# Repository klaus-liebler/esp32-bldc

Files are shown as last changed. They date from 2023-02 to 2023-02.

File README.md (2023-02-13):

# esp32-bldc - a bldc controller for stationary applications

* Main components are ESP32-S3, DRV8323HRTAR, 6x IRF7480

* Intgrated synchronous step down converter
* CAN-BUS, RS485 (both with switchable termination)
* USB-C, I2C
* All ceramic capacitors
* Power-LED
* Reset Button, Boot Button
* Thermal sensor
* breakable connector area
* optional MT6816 at the bottom PCB side
* parts available at jlcpcb, (5pcs = 113€)
* various GPIO; especially for external magnetic sensor
* desinged with [KiCad](https://www.kicad.org/) with [https://simplefoc.com/](https://simplefoc.com/) in mind
* Four mounting holes
* dimensions 60mm x 52mm (63mm with big connectors)
* currently COMPLETELY untested

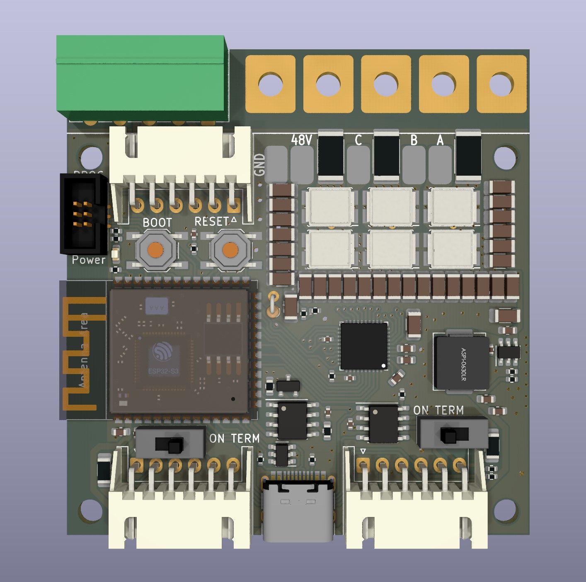
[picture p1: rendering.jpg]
This is an image


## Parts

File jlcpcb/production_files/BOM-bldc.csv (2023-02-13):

Comment | Designator | Footprint | LCSC
1k | R29 | R_0402_1005Metric | C11702
SN65HVD230 | U6 | SOIC-8_3.9x4.9mm_P1.27mm | C12084
10uH | L1 | L_Abracon_ASPI-0630LR | C132141
10u/50V | C1,C10,C11,C12,C13,C14,C15,C16,C17,C18,C19,C2,C20,C28,C29,C3,C30,C31,C32,C38,C4,C5,C6,C7,C8,C9 | C_1206_3216Metric | C13585
u1/50V | C21,C26 | C_0603_1608Metric | C14663
IRF7480M | Q1,Q2,Q3,Q4,Q5,Q6 | DirectFET_ME | C152356
u1 | C22,C27,C33,C35,C41,C42 | C_0402_1005Metric | C1525
1u/50V | C23 | C_0603_1608Metric | C15849
47n/50V | C24 | C_0603_1608Metric | C1622
USB_C_Receptacle_USB2.0 | J8 | USB_C_Receptacle_HRO_TYPE-C-31-M-12 | C165948
1k | R25,R26 | R_0603_1608Metric | C21190
Power | D7 | LED_0603_1608Metric | C2286
k1 | R11 | R_0402_1005Metric | C25076
k22 | R13 | R_0402_1005Metric | C25091
10k | R12,R18,R30,R9 | R_0402_1005Metric | C25744
15k | R7 | R_0402_1005Metric | C25756
22k | R28 | R_0402_1005Metric | C25768
47k | R6 | R_0402_1005Metric | C25792
4k7 | R14,R15 | R_0402_1005Metric | C25900
5k1 | R4,R5 | R_0402_1005Metric | C25905
TP6841S6 | U3 | TSOT-23-6 | C2844736
ESP32-S3-WROOM-1 | U2 | ESP32-S3-WROOM-1 | C2913199
RESET | SW2,SW4 | SW_SPST_TL3342 | C318884
PSM712 | D1 | SOT-23_smaller_withoutSilkscreen | C32677
1u/6V3 | C25 | C_0402_1005Metric | C52923
22u | C36,C37,C40 | C_0603_1608Metric | C59461
DRV8323HRTAR | U1 | Texas_S-PVQFN-N40_EP4.15x4.15mm_ThermalVias | C701783
R001 | R1,R2,R3 | R_2512_6332Metric | C728356
SRV05-4 | U5 | SOT-23-6 | C85364
SP3485 | U7 | SOIC-8_3.9x4.9mm_P1.27mm | C8963
GND | J15 | Steckzunge_4_8mm
K12 | R27 | R_1206_3216Metric_Pad1.30x1.75mm_HandSolder
MountingHole | H2 | MountingHole_3.2mm_M3_DIN965
ON TERM | SW1 | Switch_SS12D00
K12 | R10 | R_1206_3216Metric_Pad1.30x1.75mm_HandSolder
PROG | J7 | IDC_2x03_P1.27mm_Vertical
C | J13 | Steckzunge_4_8mm
MountingHole | H4 | MountingHole_3.2mm_M3_DIN965
48V | J14 | Steckzunge_4_8mm
GND | J5 | SolderWirePad_1x01_SMD_3x5mm
EXT_MAG | J16 | PhoenixContact_MC_1,5_5-G-3.81_1x05_P3.81mm_Horizontal
Thermistor | TH1 | R_Axial_DIN0204_L3.6mm_D1.6mm_P1.90mm_Vertical
MountingHole | H1 | MountingHole_3.2mm_M3_DIN965
MountingHole | H3 | MountingHole_3.2mm_M3_DIN965
ON TERM | SW3 | Switch_SS12D00
EXT_MAG | J6 | JST_XH_S6B-XH-A_1x06_P2.50mm_Horizontal
B | J2 | SolderWirePad_1x01_SMD_3x5mm
A | J11 | Steckzunge_4_8mm
Conn_01x06 | J10 | JST_XH_S6B-XH-A_1x06_P2.50mm_Horizontal
B | J12 | Steckzunge_4_8mm
NUP2105 | D6 | SOT-23_Handsoldering
C | J3 | SolderWirePad_1x01_SMD_3x5mm
A | J1 | SolderWirePad_1x01_SMD_3x5mm
48V | J4 | SolderWirePad_1x01_SMD_3x5mm
Conn_01x06 | J9 | JST_XH_S6B-XH-A_1x06_P2.50mm_Horizontal
xxk | R20 | R_0805_2012Metric_Pad1.20x1.40mm_HandSolder
GHB | TP3 | TestPoint_THTPad_D1.0mm_Drill0.5mm
yyk | R16 | R_0805_2012Metric_Pad1.20x1.40mm_HandSolder
xxk | R22 | R_0805_2012Metric_Pad1.20x1.40mm_HandSolder
GHC | TP5 | TestPoint_THTPad_D1.0mm_Drill0.5mm
xxk | R17 | R_0805_2012Metric_Pad1.20x1.40mm_HandSolder
GHA | TP1 | TestPoint_THTPad_D1.0mm_Drill0.5mm
yyk | R23 | R_0805_2012Metric_Pad1.20x1.40mm_HandSolder
yyk | R19 | R_0805_2012Metric_Pad1.20x1.40mm_HandSolder
xxk | R24 | R_0805_2012Metric_Pad1.20x1.40mm_HandSolder
u1 | C34 | C_0805_2012Metric_Pad1.18x1.45mm_HandSolder
GLC | TP6 | TestPoint_THTPad_D1.0mm_Drill0.5mm
GLB | TP4 | TestPoint_THTPad_D1.0mm_Drill0.5mm
MT6816 | U4 | SO-8_3.9x4.9mm_P1.27mm
yyk | R21 | R_0805_2012Metric_Pad1.20x1.40mm_HandSolder
GLA | TP2 | TestPoint_THTPad_D1.0mm_Drill0.5mm

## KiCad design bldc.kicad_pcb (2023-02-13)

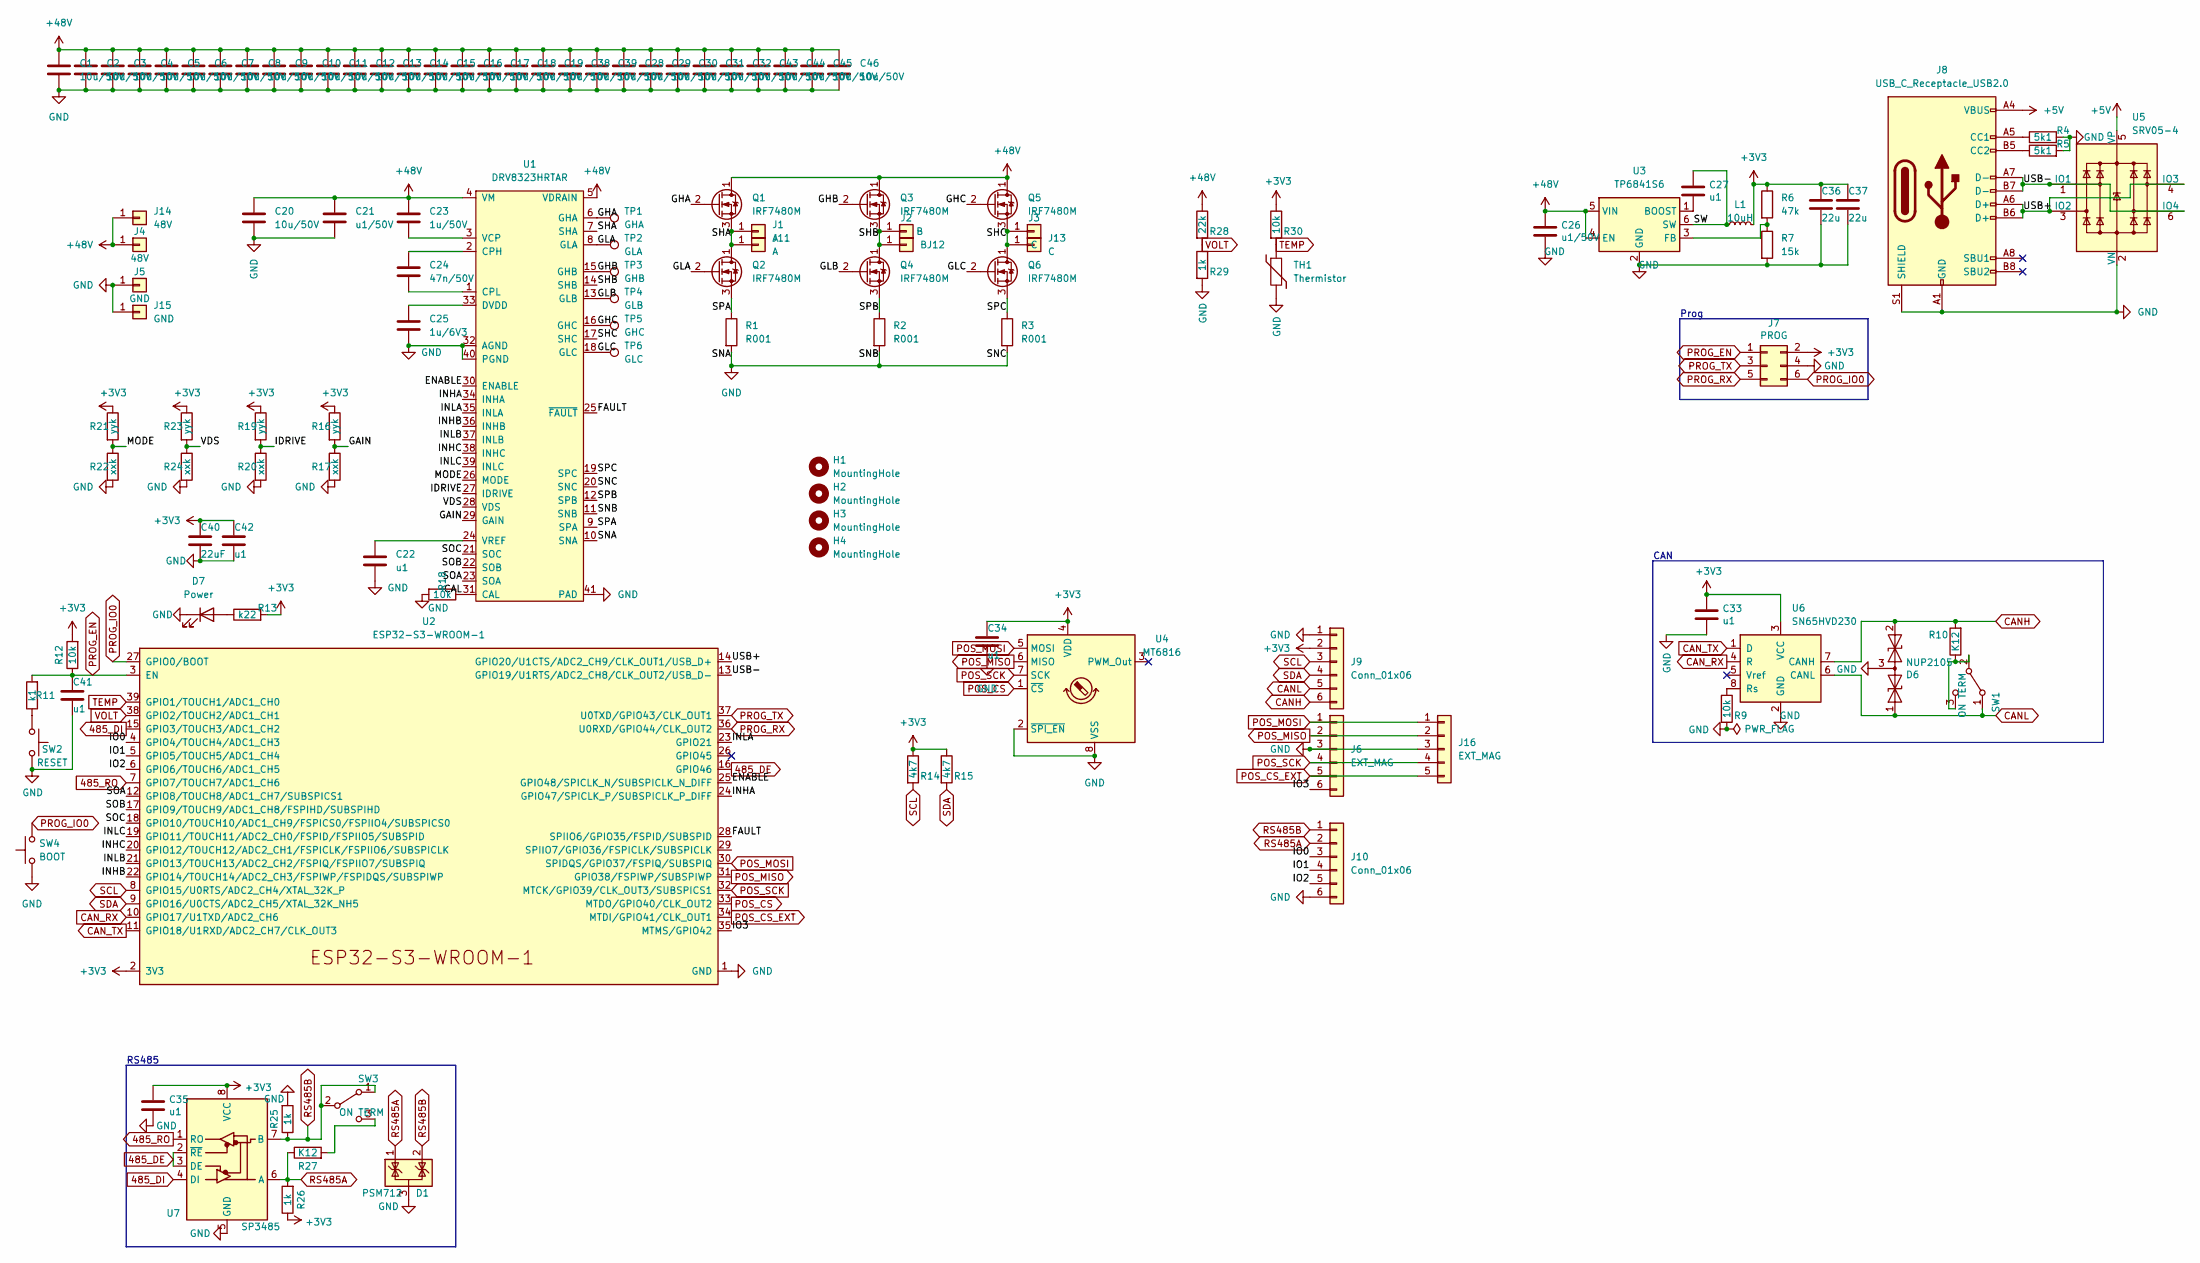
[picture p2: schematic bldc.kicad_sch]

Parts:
C1, C2, C3, C4, C5, C6, C7, C8, C9, C10, C11, C12, C13, C14, C15, C16, C17, C18, C19, C28, C29, C30, C31, C32, C38, C39, C43, C44, C45, C46: 10u/50V; C_1206_3216Metric_smaller
C20: 10u/50V; C_1206_3216Metric
C21, C26: u1/50V; C_0603_1608Metric
C22, C27, C33, C35, C41, C42: u1; C_0402_1005Metric
C23: 1u/50V; C_0603_1608Metric
C24: 47n/50V; C_0603_1608Metric
C25: 1u/6V3; C_0402_1005Metric
C34: u1; C_0805_2012Metric_Pad1.18x1.45mm_HandSolder
C36, C37: 22u; C_0603_1608Metric
C40: 22uF; C_0603_1608Metric
D1: PSM712; SOT-23_smaller_withoutSilkscreen
D6: NUP2105; SOT-23_Handsoldering
D7: Power; LED_0603_1608Metric
H1, H2, H3, H4: MountingHole; MountingHole_3.2mm_M3_DIN965
J1: A; SolderWirePad_1x01_SMD_3x5mm
J2: B; SolderWirePad_1x01_SMD_3x5mm
J3: C; SolderWirePad_1x01_SMD_3x5mm
J4: 48V; SolderWirePad_1x01_SMD_3x5mm
J5: GND; SolderWirePad_1x01_SMD_3x5mm
J6: EXT_MAG; JST_XH_S6B-XH-A_1x06_P2.50mm_Horizontal
J7: PROG; IDC_2x03_P1.27mm_Vertical
J8: USB_C_Receptacle_USB2.0; USB_C_Receptacle_HRO_TYPE-C-31-M-12
J9, J10: Conn_01x06; JST_XH_S6B-XH-A_1x06_P2.50mm_Horizontal
J11: A; Steckzunge_4_8mm
J12: B; Steckzunge_4_8mm
J13: C; Steckzunge_4_8mm
J14: 48V; Steckzunge_4_8mm
J15: GND; Steckzunge_4_8mm
J16: EXT_MAG; PhoenixContact_MC_1,5_5-G-3.81_1x05_P3.81mm_Horizontal
L1: 10uH; L_Abracon_ASPI-0630LR
Q1, Q2, Q3, Q4, Q5, Q6: IRF7480M; DirectFET_ME
R1, R2, R3: R001; R_2512_6332Metric
R4, R5: 5k1; R_0402_1005Metric
R6: 47k; R_0402_1005Metric
R7: 15k; R_0402_1005Metric
R9, R12, R18, R30: 10k; R_0402_1005Metric
R10, R27: K12; R_1206_3216Metric_Pad1.30x1.75mm_HandSolder
R11: k1; R_0402_1005Metric
R13: k22; R_0402_1005Metric
R14, R15: 4k7; R_0402_1005Metric
R16, R19, R21, R23: yyk; R_0805_2012Metric_Pad1.20x1.40mm_HandSolder
R17, R20, R22, R24: xxk; R_0805_2012Metric_Pad1.20x1.40mm_HandSolder
R25, R26: 1k; R_0603_1608Metric
R28: 22k; R_0402_1005Metric
R29: 1k; R_0402_1005Metric
SW1, SW3: ON TERM; Switch_SS12D00
SW2: RESET; SW_SPST_TL3342
SW4: BOOT; SW_SPST_TL3342
TH1: Thermistor; R_Axial_DIN0204_L3.6mm_D1.6mm_P1.90mm_Vertical
TP1: GHA; TestPoint_THTPad_D1.0mm_Drill0.5mm
TP2: GLA; TestPoint_THTPad_D1.0mm_Drill0.5mm
TP3: GHB; TestPoint_THTPad_D1.0mm_Drill0.5mm
TP4: GLB; TestPoint_THTPad_D1.0mm_Drill0.5mm
TP5: GHC; TestPoint_THTPad_D1.0mm_Drill0.5mm
TP6: GLC; TestPoint_THTPad_D1.0mm_Drill0.5mm
U1: DRV8323HRTAR; Texas_S-PVQFN-N40_EP4.15x4.15mm_ThermalVias
U2: ESP32-S3-WROOM-1
U3: TP6841S6; TSOT-23-6
U4: MT6816; SO-8_3.9x4.9mm_P1.27mm
U5: SRV05-4; SOT-23-6
U6: SN65HVD230; SOIC-8_3.9x4.9mm_P1.27mm
U7: SP3485; SOIC-8_3.9x4.9mm_P1.27mm

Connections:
485_DE: U2.16 (GPIO46), U7.2 (~RE), U7.3 (DE)
485_DI: U2.15 (GPIO3/TOUCH3/ADC1_CH2), U7.4 (DI)
485_RO: U2.7 (GPIO7/TOUCH7/ADC1_CH6), U7.1 (RO)
+3V3: C33.1, C34.2, C35.2, C36.1, C37.1, C40.1, C42.2, J7.2, J9.2, L1.2, R6.1, R12.2, R13.2, R14.1, R15.1, R16.1, R19.1, R21.1, R23.1, R26.1, R30.1, U2.2 (3V3), U4.4 (VDD), U6.3 (VCC), U7.8 (VCC)
+5V: J8.A4 (VBUS), J8.A9 (VBUS), J8.B4 (VBUS), J8.B9 (VBUS), U5.5 (VP)
+48V: C1.1, C2.1, C3.1, C4.1, C5.1, C6.1, C7.1, C8.1, C9.1, C10.1, C11.1, C12.1, C13.1, C14.1, C15.1, C16.1, C17.1, C18.1, C19.1, C20.2, C21.1, C23.1, C26.1, C28.1, C29.1, C30.1, C31.1, C32.1, C38.1, C39.1, C43.1, C44.1, C45.1, C46.1, J4.1, J14.1, Q1.1 (D), Q3.1 (D), Q5.1 (D), R28.1, U1.4 (VM), U1.5 (VDRAIN), U3.4 (EN), U3.5 (VIN)
/CAL: R18.1, U1.31 (CAL)
/ENABLE: U1.30 (ENABLE), U2.25 (GPIO48/SPICLK_N/SUBSPICLK_N_DIFF)
/FAULT: U1.25 (~FAULT), U2.28 (SPIIO6/GPIO35/FSPID/SUBSPID)
/GAIN: R16.2, R17.1, U1.29 (GAIN)
/GHA: Q1.2 (G), TP1.1, U1.6 (GHA)
/GHB: Q3.2 (G), TP3.1, U1.15 (GHB)
/GHC: Q5.2 (G), TP5.1, U1.16 (GHC)
/GLA: Q2.2 (G), TP2.1, U1.8 (GLA)
/GLB: Q4.2 (G), TP4.1, U1.13 (GLB)
/GLC: Q6.2 (G), TP6.1, U1.18 (GLC)
/IDRIVE: R19.2, R20.1, U1.27 (IDRIVE)
/INHA: U1.34 (INHA), U2.24 (GPIO47/SPICLK_P/SUBSPICLK_P_DIFF)
/INHB: U1.36 (INHB), U2.22 (GPIO14/TOUCH14/ADC2_CH3/FSPIWP/FSPIDQS/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)
/INHC: U1.38 (INHC), U2.20 (GPIO12/TOUCH12/ADC2_CH1/FSPICLK/FSPIIO6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)
/INLA: U1.35 (INLA), U2.23 (GPIO21)
/INLB: U1.37 (INLB), U2.21 (GPIO13/TOUCH13/ADC2_CH2/FSPIQ/FSPIIO7/S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)
/INLC: U1.39 (INLC), U2.19 (GPIO11/TOUCH11/ADC2_CH0/FSPID/FSPIIO5/S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)
/IO0: J10.3, U2.4 (GPIO4/TOUCH4/ADC1_CH3)
/IO1: J10.4, U2.5 (GPIO5/TOUCH5/ADC1_CH4)
/IO2: J10.5, U2.6 (GPIO6/TOUCH6/ADC1_CH5)
/IO3: J6.6, U2.35 (MTMS/GPIO42)
/MODE: R21.2, R22.1, U1.26 (MODE)
/SHA: J1.1, J11.1, Q1.3 (S), Q2.1 (D), U1.7 (SHA)
/SHB: J2.1, J12.1, Q3.3 (S), Q4.1 (D), U1.14 (SHB)
/SHC: J3.1, J13.1, Q5.3 (S), Q6.1 (D), U1.17 (SHC)
/SOA: U1.23 (SOA), U2.12 (GPIO8/TOUCH8/ADC1_CH7/SUBSPICS1)
/SOB: U1.22 (SOB), U2.17 (GPIO9/TOUCH9/ADC1_CH8/FSPIHD/SUBSPIHD)
/SOC: U1.21 (SOC), U2.18 (GPIO10/TOUCH10/ADC1_CH9/FSPICS0/FSPIIO4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)
/SPA: Q2.3 (S), R1.1, U1.9 (SPA)
/SPB: Q4.3 (S), R2.1, U1.12 (SPB)
/SPC: Q6.3 (S), R3.1, U1.19 (SPC)
/SW: C27.1, L1.1, U3.6 (SW)
/USB+: J8.A6 (D+), J8.B6 (D+), U2.14 (GPIO20/U1CTS/ADC2_CH9/CLK_OUT1/USB_D+), U5.3 (IO2), U5.4 (IO3)
/USB-: J8.A7 (D-), J8.B7 (D-), U2.13 (GPIO19/U1RTS/ADC2_CH8/CLK_OUT2/USB_D-), U5.1 (IO1), U5.6 (IO4)
/VDS: R23.2, R24.1, U1.28 (VDS)
CANH: D6.2 (A2), J9.6, R10.2, U6.7 (CANH)
CANL: D6.1 (A1), J9.5, SW1.1 (A), U6.6 (CANL)
CAN_RX: U2.10 (GPIO17/U1TXD/ADC2_CH6), U6.4 (R)
CAN_TX: U2.11 (GPIO18/U1RXD/ADC2_CH7/CLK_OUT3), U6.1 (D)
GND: C1.2, C2.2, C3.2, C4.2, C5.2, C6.2, C7.2, C8.2, C9.2, C10.2, C11.2, C12.2, C13.2, C14.2, C15.2, C16.2, C17.2, C18.2, C19.2, C20.1, C21.2, C22.2, C25.2, C26.2, C28.2, C29.2, C30.2, C31.2, C32.2, C33.2, C34.1, C35.1, C36.2, C37.2, C38.2, C39.2, C40.2, C41.2, C42.1, C43.2, C44.2, C45.2, C46.2, D1.3 (A), D6.3 (common), D7.1 (K), J5.1, J6.3, J7.4, J8.A1 (GND), J8.A12 (GND), J8.B1 (GND), J8.B12 (GND), J8.S1 (SHIELD), J9.1, J10.6, J15.1, J16.3, R1.2, R2.2, R3.2, R4.2, R5.2, R7.2, R9.2, R17.2, R18.2, R20.2, R22.2, R24.2, R25.2, R29.2, SW2.2, SW4.1, TH1.2, U1.10 (SNA), U1.11 (SNB), U1.20 (SNC), U1.32 (AGND), U1.40 (PGND), U1.41 (PAD), U2.1 (GND), U2.40 (GND), U2.41 (GND), U3.2 (GND), U4.2 (~SPI_EN), U4.8 (VSS), U5.2 (VN), U6.2 (GND), U7.5 (GND)
unnamed: C22.1, U1.24 (VREF)
unnamed: C23.2, U1.3 (VCP)
unnamed: C24.1, U1.2 (CPH)
unnamed: C24.2, U1.1 (CPL)
unnamed: C25.1, U1.33 (DVDD)
unnamed: C27.2, U3.1 (BOOST)
unnamed: D7.2 (A), R13.1
unnamed: J8.A5 (CC1), R4.1
unnamed: J8.B5 (CC2), R5.1
unnamed: R6.2, R7.1, U3.3 (FB)
unnamed: R9.1, U6.8 (Rs)
unnamed: R10.1, SW1.2 (B), SW1.3 (C)
unnamed: R11.1, SW2.1
unnamed: R27.2, SW3.3 (C)
POS_CS: U2.33 (MTDO/GPIO40/CLK_OUT2), U4.1 (~CS)
POS_CS_EXT: J6.5, J16.5, U2.34 (MTDI/GPIO41/CLK_OUT1)
POS_MISO: J6.2, J16.2, U2.31 (GPIO38/FSPIWP/SUBSPIWP), U4.6 (MISO)
POS_MOSI: J6.1, J16.1, U2.30 (SPIDQS/GPIO37/FSPIQ/SUBSPIQ), U4.5 (MOSI)
POS_SCK: J6.4, J16.4, U2.32 (MTCK/GPIO39/CLK_OUT3/SUBSPICS1), U4.7 (SCK)
PROG_EN: C41.1, J7.1, R11.2, R12.1, U2.3 (EN)
PROG_IO0: J7.6, SW4.2, U2.27 (GPIO0/BOOT)
PROG_RX: J7.5, U2.36 (U0RXD/GPIO44/CLK_OUT2)
PROG_TX: J7.3, U2.37 (U0TXD/GPIO43/CLK_OUT1)
RS485A: D1.1 (K), J10.2, R26.2, R27.1, U7.6 (A)
RS485B: D1.2 (K), J10.1, R25.1, SW3.1 (A), SW3.2 (B), U7.7 (B)
SCL: J9.3, R14.2, U2.8 (GPIO15/U0RTS/ADC2_CH4/XTAL_32K_P)
SDA: J9.4, R15.2, U2.9 (GPIO16/U0CTS/ADC2_CH5/XTAL_32K_NH5)
TEMP: R30.2, TH1.1, U2.39 (GPIO1/TOUCH1/ADC1_CH0)
VOLT: R28.2, R29.1, U2.38 (GPIO2/TOUCH2/ADC1_CH1)

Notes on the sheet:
RS485
CAN
Prog

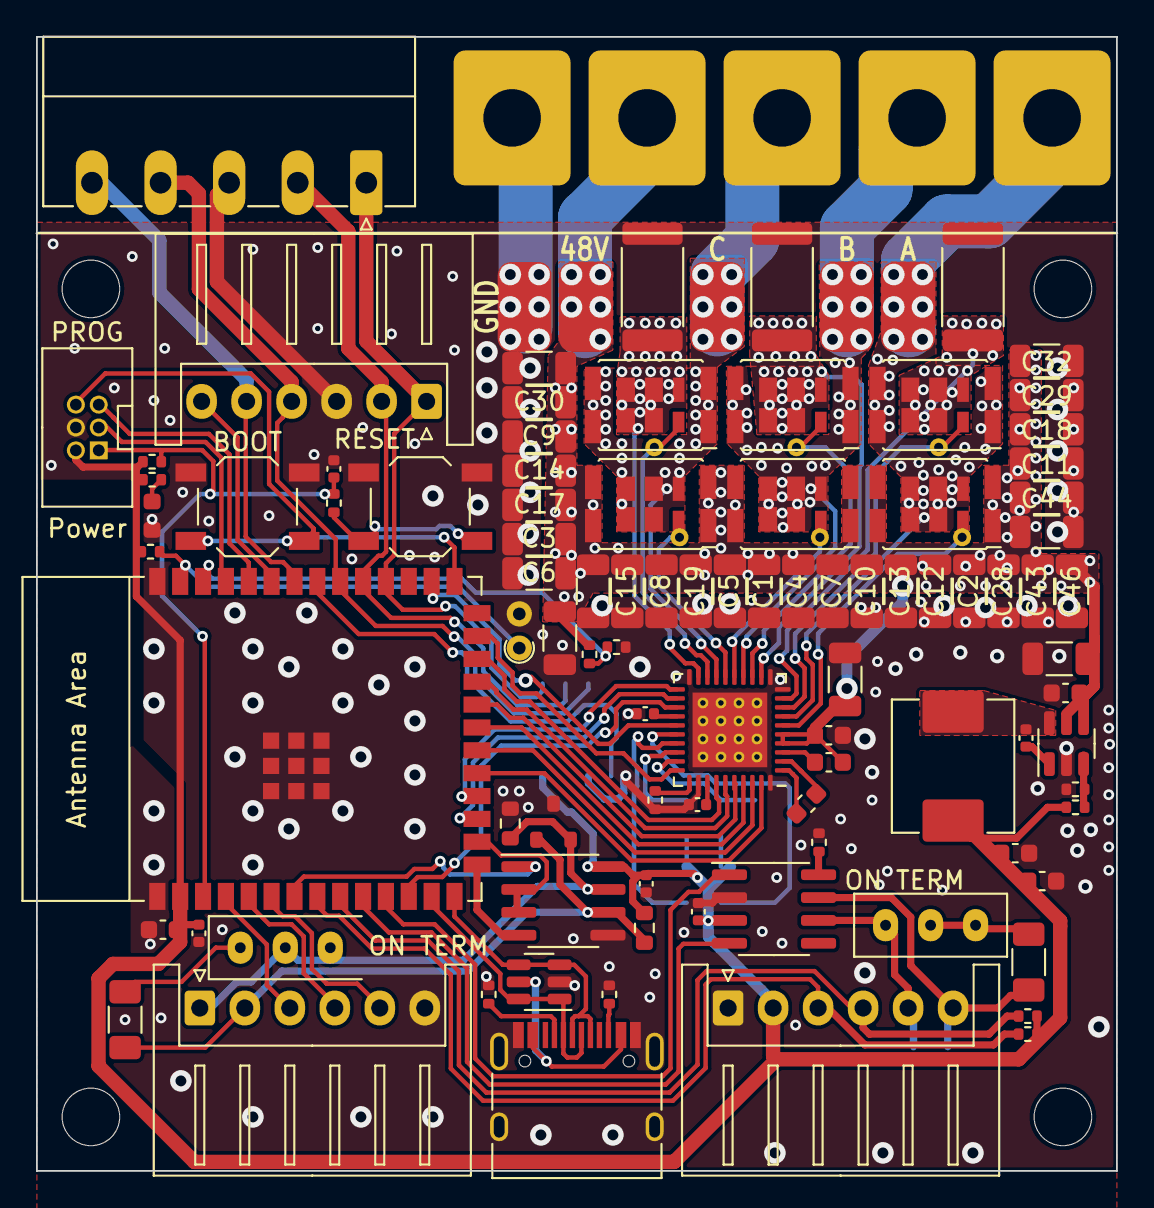
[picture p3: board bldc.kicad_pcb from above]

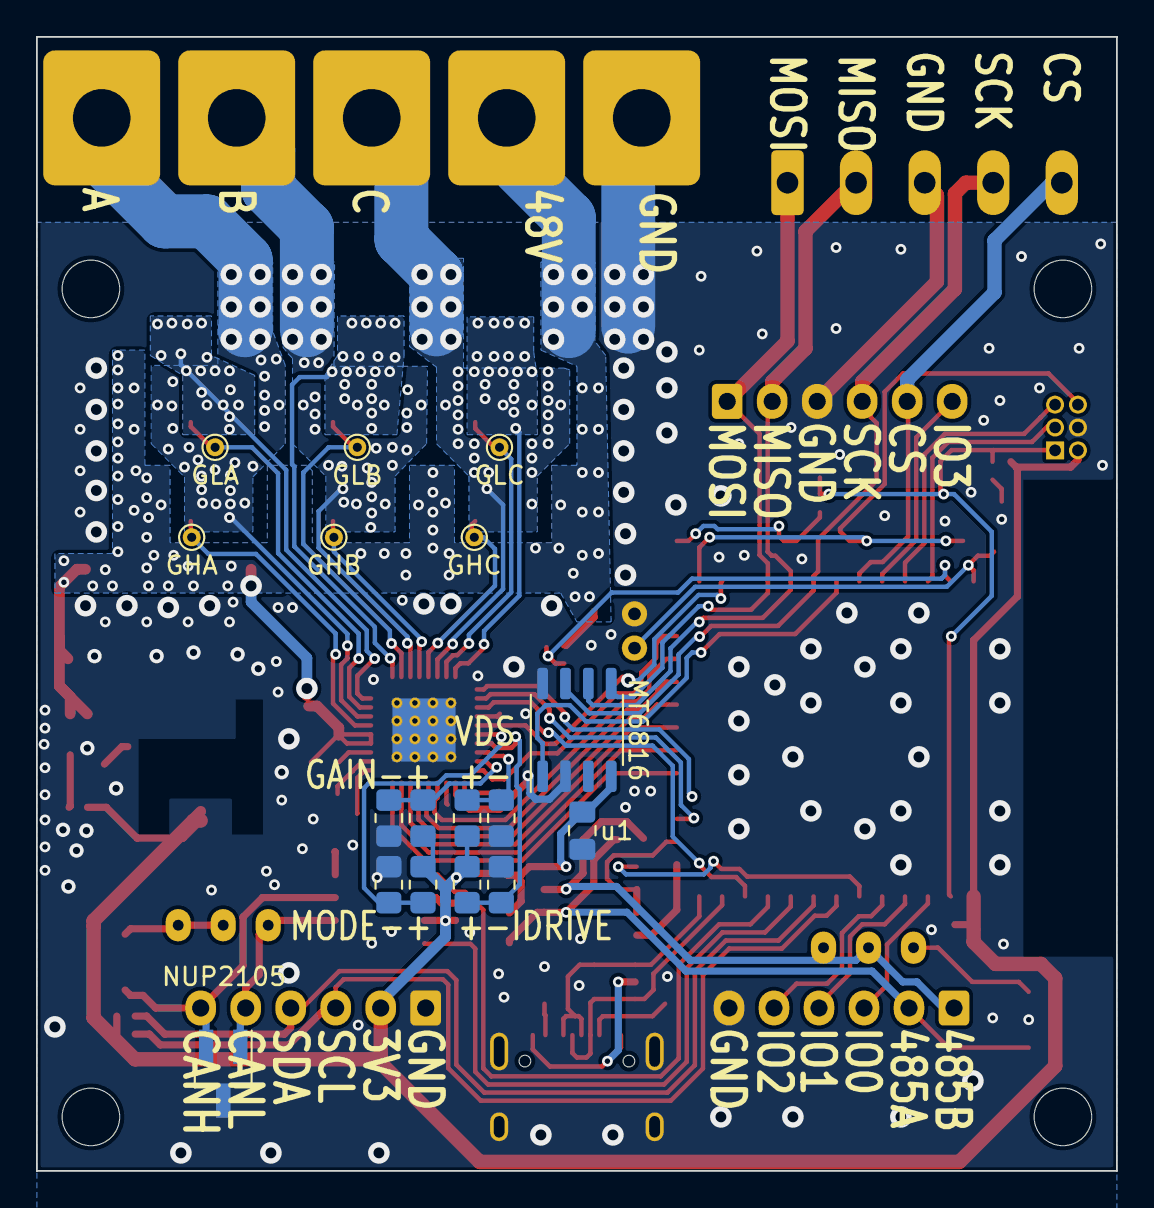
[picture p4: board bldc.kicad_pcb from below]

Board: 2 copper layers, 60.0 x 63.0 mm, 123 parts (17 on the bottom side), 75 nets.
